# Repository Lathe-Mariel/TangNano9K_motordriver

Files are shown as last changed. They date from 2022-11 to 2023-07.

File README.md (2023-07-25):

# TangNano9K_Motordriver Board
  
Tang Nano 9K(Sipeed)用のマザーボード（拡張ボード）です．  
This is mother board for Tang Nano 9K(Sipeed).  

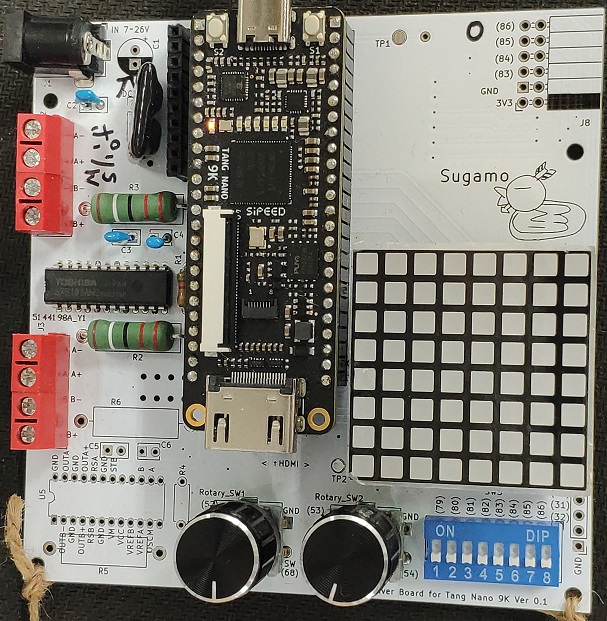
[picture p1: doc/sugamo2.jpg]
MotorDriver board for TangNano 9K
  
  
オープンソースの回路CADである，KiCAD のプロジェクトになっています．  
These files were made by KiCAD.
  
/doc ドキュメント用の素材  
/output　KiCADで出力したガーバーデータ  
/output/tangnano9k_motordriver-v3.zip　　PCBメーカにアップロードするファイル  
/sampleProject　この基板向けの数種類のサンプルプロジェクト  

## 機能 Functions
次の機能を実装できます．
- ステッピングモータドライバ x2ch <TB67S101ANG(TOSHIBA)>
- ロータリエンコーダ x2
- 8x8 マトリクスLED <OSL641501-BRA(Optsupply)>
- 7セグメントLED
- DIP Switch(8ch)

You can install these functions with this board.
- Stepper motor driver x2ch
- Rotary encoder x2
- 8x8 Matrix LED
- 7segment LED
- DIP Switch(8ch)

## 電源 Power supply
ボード上にDC-DCコンバータBP5293-50(ROHM)を実装できます．  
DC-DCコンバータには7～26Vを入力し，出力される5VをTang Nano 9Kへ供給できます．  
DC-DC converter can be installed on the board.  
  
基板上のDCジャックへ入力された電圧は，上記DC-DCコンバータとモータ・ドライバICのモータ電源（VM）へ入力されます．  
 
## FPGA側のピンを共用する機能 Multi purpose pins for board functions
　FPGAのピン数が限られているので，拡張ボードの持つ機能のうち，一部の機能は同時利用はできません．  
   
### HDMIコネクタとマトリクスLED＆ロータリ・エンコーダ×2
　DVI信号を出力する場合， `HDMI_CK_N(68)` ， `HDMI_CK_P(69)` ， `HDMI_D0` ～ `HDMI_D2` など8本の信号を使います．これらは，ロータリ・エンコーダ2ch目およびマトリクスLEDの信号と競合します．従ってDVI出力する場合は，ロータリ・エンコーダの2ch目とマトリクスLEDが使えません．  
  ボードにマトリクスLEDを実装するときは，必要に応じて脱着できるようにピンソケット経由にするのがお勧めです． 

### HDMIコネクタとマトリクスLED
　一部の信号を共有しています．HDMIコネクタから信号を出す場合はマトリクスLEDを取り付けない方がよいでしょう．  
 マトリクスLEDを実装するときは，ピンソケットを介して取り付けるのがお勧めです．そうすれば，マトリクスLEDを必要に応じて脱着できます．  
  
### 排他利用する機能の選択 Selection of exclusive functions
　モータドライバの励磁モード選択は `INA1` ， `INA2` ， `INB1` ， `INB2` 端子で行います．  
　2CH目（基板下側）のモータドライバは，ソルダジャンパ `JP1～JP4` をショートすると， `INA1～INB2` の全てがVCCに接続され，励磁モードが2相励磁に固定されます（この場合， `JP5～JP8` はオープンのままにする）．   
 　2ch目のモータドライバで1-2相励磁やW1-2相励磁を行いたい場合，ソルダジャンパ `JP5～JP8` をショートさせます．すると `INA1～INB2` がFPGAに接続されるので，FPGAからHi/Lowを制御できます．  
  　ちなみに1ch目のモータドライバについては，このようなソルダジャンパはありません． `INA1～INB2` は全てFPGAに直結されているので，どの様な励磁モードを使う場合でも，FPGAから制御する必要があります．  
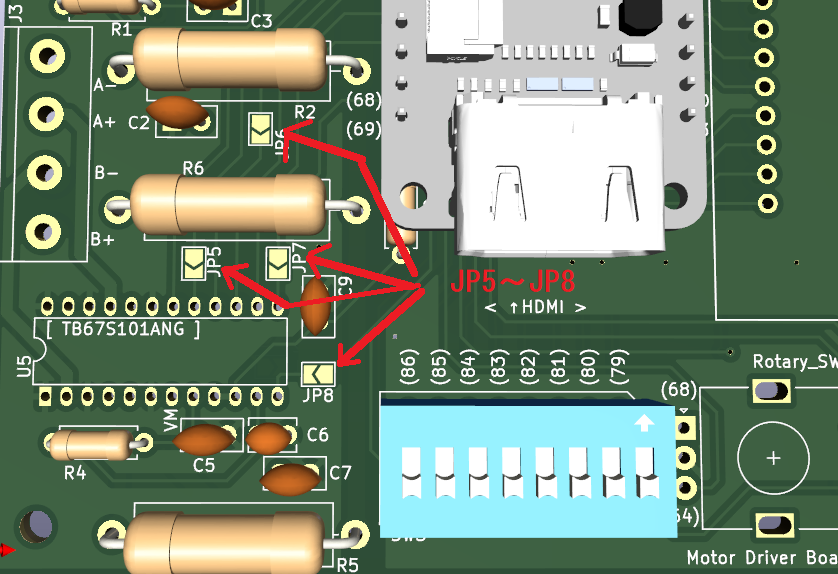
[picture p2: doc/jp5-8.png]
ソルダジャンパで選択する
  
  FPGA側では，これらの端子をロータリエンコーダの2ch目と共有しています．  
  従って，モータドライバの2ch目の1-2相励磁選択と，ロータリエンコーダの2ch目は排他利用となります．  
#### 設定例
　①例えば，モータドライバを1chしか使わない場合は， `JP1～JP8` のソルダジャンパをオープンのまま使用します（7セグLEDを使うなら `JP9` のみショートする）．  
 　②例えば，モータドライバの2ch目を1-2相励磁（あるいはW1-2相励磁）で使いたい場合は， `JP5～JP8` のソルダジャンパをショートします（ `INA1～INB2` がFPGAと直結される）．  
  この場合7セグLEDとロータリエンコーダの2ch目は使用できません（実装もしない方がよいでしょう）．  

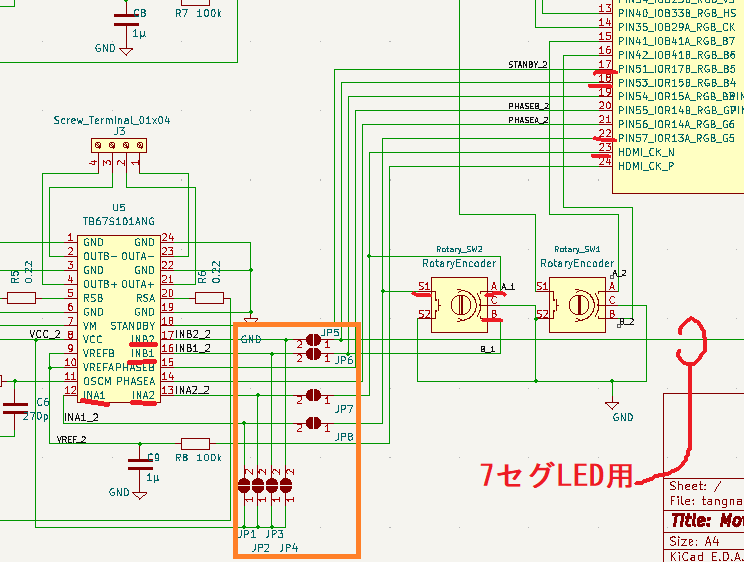
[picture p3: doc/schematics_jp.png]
JP1～JP4またはJP5～JP8のどちらかのセットをショートさせる

- JP1 ～ JP4　　ショートさせるとINA1～INB2をTB67S101ANGのVCCピンと接続
- JP5 ～ JP8　　ショートさせるとFPGAとINA1～INB2を接続
- JP9　　JP5の線を7セグLEDのコモンに接続
- JP10 ～ JP17　　マトリクスLEDに（アノード側）電流制限抵抗を付けない場合は，これらのソルダージャンパをショートさせてください  

## マトリクスLED MatrixLED
　~増幅回路も電流制限抵抗も入れていません．~  
　~ワイルドだろぅ？~  
  電流制限抵抗を入れない場合は，ソルダージャンパ `JP10` ～ `JP17` をジャンパします．
　必要であれば，FPGA側のロジックで絞ってください．  
　特に絞らずに使っていますが，LEDもFPGAも壊れないようです．  
  
  電流制限抵抗を入れる場合は，ソルダージャンパ `JP10` ～ `JP17` はオープンなまま抵抗器を実装します．  
トランジスタなどのパターンは基板にありません．電流を増幅せずに，真面目に計算して電流制限抵抗を入れると，LEDがかなり暗くなるようです．  

### マトリクスLED取り付け向き
  LED_direction

## 部品
　思いつく限り列挙．抜けがあるかもしれない．  
 ロータリエンコーダのみ，押しスイッチ付きのものが秋月さんに見当たらなかったので，リストに入っていません．  
 基板の4角には穴が開いています．足としてM3程度のボルト・ナットを用意するとよいでしょう．M3だときついのですが，ねじ込めば入ります．  
 （モータドライブ回路用の部品は1ch分の数量を掲載している）
　ちなみに，秋月さんの店頭に出ていない部品もあります（モータドライバなどは，裏オプションなので，お店の人に言うと裏から出してくれます）．
   
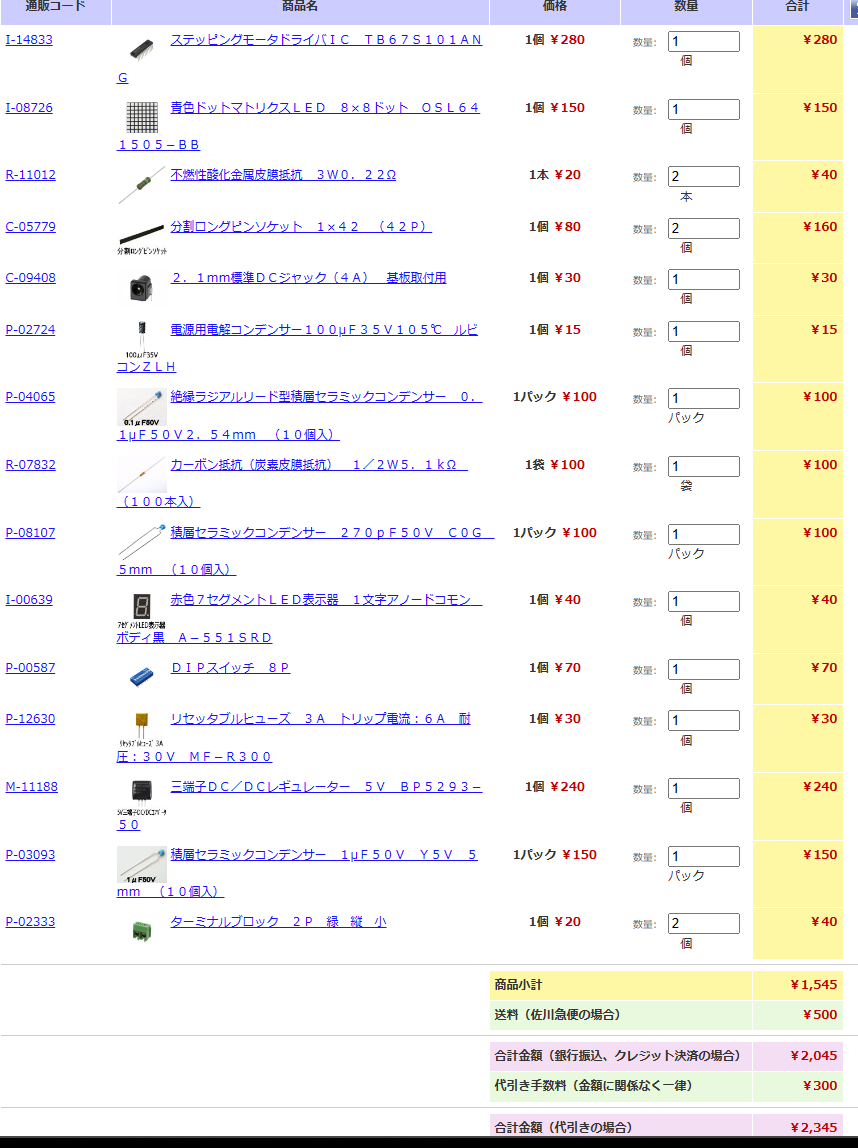
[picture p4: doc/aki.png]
参考部品リスト
 
 
## 機能の補足 Additional for Functions
### モータドライバTB67S101ANG（TOSHIBA）
　このICへ電流制御用のレファレンス電圧を供給する必要があります．Pinは `VREFA` 及び `VREFB` です．このボードでは `VREFA` と `VREFB` は直結されています．これらとFPGAの `27` （モータドライバch1）が接続されています．FPGAからパルスのデューティで所望の電圧を送って下さい．電圧の平滑化のために，RCフィルタのパターンが実装されています．R7とC8（モータドライバch1）に適当な値のものを実装してください．  
 （RCは，1μFと100kオーム．duty3/8くらいから試してください）  

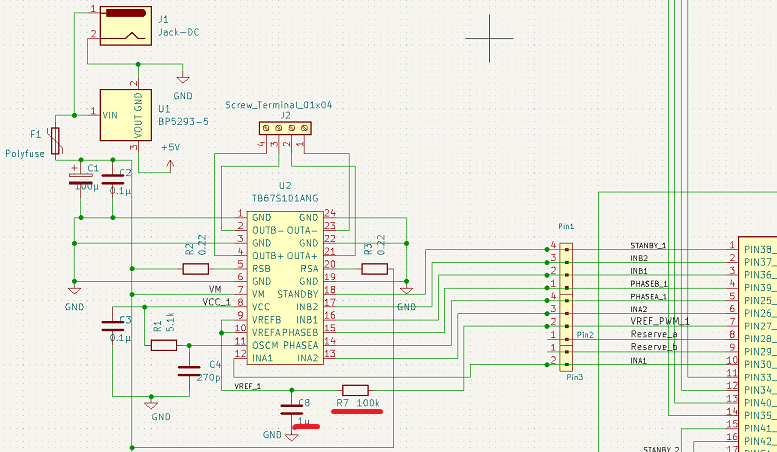
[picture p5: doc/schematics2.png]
モータドライバのレファレンス電圧供給経路にあるRCフィルタ
   

## サンプルプログラム
   
### PolyphonyMatrix_Clock
`/sampleProject`にマトリクスLEDを使った時計のプロジェクトが入っています．  
このプロジェクトはPythonベースの高位合成ツールPolyphonyを利用しています．  
　Gowin EDAのプロジェクトになっているので，そのままGowin EDAで読み込めます．impl/pnr/にビットストリームファイルもあるので，合成しなくてもすぐにFlash Programmerで書き込めます．  
 Verilogファイル `LEDMatrixAB_m.v` は，Polyphonyで `LEDMatrix.py` をコンパイルして生成したものです．
 
### MotorDriver
 モータドライバ IC TB67S101ANG(TOSHIBA) を使ってステッピングモータの2相励磁，1－2相励磁，W1-2相励磁ができます． 
 このサンプルプログラムでは，DVI出力もしています．ピンが競合するのでマトリクスLEDは取り外してください．  
#### DVI出力
　DVI出力については，Interface誌2022年12月号　別冊付録Gowin　の応用編第3章の記事で紹介されたデザインをパクり，一部を改変しています（SPDXライセンス）．  

### Parallel
　回路を複数のモジュールに分けて並列に実行させるサンプルです．3つのLEDを3つの回路で点滅させています．  
  
 （1）TB67S101ANGデータシート  
 https://toshiba.semicon-storage.com/jp/semiconductor/product/motor-driver-ics/stepping-motor-driver-ics/detail.TB67S101ANG.html

# Schematics
https://kicanvas.org/?github=https%3A%2F%2Fgithub.com%2FLathe-Mariel%2FTangNano9K_motordriver%2Ftree%2Fmain

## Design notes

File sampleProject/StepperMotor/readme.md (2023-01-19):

  
## 励磁モードは3つ用意してある There're 3types of excitation mode
|File|content|
|---|---|
src/Motor_12.sv | 1－2相励磁　駆動モジュール  
src/Motor_w12.sv | W1－2相励磁　駆動モジュール  
src/Motor_2.sv | 2相励磁　駆動モジュール  
src/top_w12.sv | トップモジュール  
src/top.cst | MotorDriver Board for TangNano9K用物理制約ファイル  
src/StepperMotor.rao | 
impl/pnr/a0_0.fs | GAO用ビットストリーム
impl/pnr/StepperMotor.fs | ビットストリーム
  
3つある駆動モジュールのインターフェースは全て同じなので容易に入れ替えできます．  
Because of same interface, You can easily swap motor driver module.  
  
### 駆動モジュールのインターフェース

  input  wire       clk,　　システムクロック（←トップモジュール）  
  output logic      phase_a,　　A相コイル（→ドライバIC）  
  output logic      phase_b,　　B相コイル（→ドライバIC）  
  output logic      INB1,　　INB1信号（→ドライバIC）  
  output logic      INB2,　　INB2信号（→ドライバIC）  
  output logic      INA1,　　INA1信号（→ドライバIC）  
  output logic      INA2,　　INA2信号（→ドライバIC）  
  output logic      STANBY,　　スタンバイ（→ドライバIC）　ONでドライバICがレディ（レディ状態で，回転指令がないの場合はロータ位置を保持）  
  output logic      VREF_PWM,　　電流設定用の電圧をdutyで出力（→ドライバIC）　ボード上にRCフィルタ有り  
  input  wire       rotate_pulse,　　回転速度指令（←トップモジュール）  
  input  wire       direction,　　回転方向指令  （←トップモジュール）  
  input  wire       module_enable,　　モジュール・イネーブル指令（←トップモジュール）  
  input  wire[3:0]       vref_level　　駆動電流値指令　｛0～15の16段階｝  （←トップモジュール）  
    
  モジュールへの指令は下段の4つの信号で行います．  
  top.svモジュールからこの4つの信号を使って指令すれば，このモジュール内でモータドライバICへ送る信号が生成されます．  

ステッピングモータの回転　1ステップを `rotate_pulse` で指令します．  
3つある駆動モジュールそれぞれの1ステップに対する機械角は1：2：4（2相/1-2相/W1-2相）になります．  
これらを統一するため， `Motor_2.sv` モジュール内では， `rotate_pulse` を4分周しています．  
同様に， `Motor_12.sv` モジュール内では2分周しています．  
これによって，どのモジュールであっても，同じ周波数のパルスを `rotate_pulse` に与えれば，モータは同じ機械角速度で回転します．

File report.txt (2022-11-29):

Info: Processing symbol 'C1:Capacitor_THT:CP_Radial_D5.0mm_P2.50mm'.
Info: Processing symbol 'C6:Capacitor_THT:C_Disc_D3.8mm_W2.6mm_P2.50mm'.
Info: Processing symbol 'SW3:Button_Switch_THT:SW_DIP_SPSTx08_Slide_9.78x22.5mm_W7.62mm_P2.54mm'.
Info: Processing symbol 'J6:Connector_PinHeader_2.54mm:PinHeader_1x02_P2.54mm_Vertical'.
Info: Processing symbol 'C4:Capacitor_THT:C_Disc_D3.8mm_W2.6mm_P2.50mm'.
Info: Processing symbol 'R2:Resistor_THT:R_Axial_DIN0516_L15.5mm_D5.0mm_P20.32mm_Horizontal'.
Info: Processing symbol 'R3:Resistor_THT:R_Axial_DIN0516_L15.5mm_D5.0mm_P20.32mm_Horizontal'.
Info: Processing symbol 'R1:Resistor_THT:R_Axial_DIN0207_L6.3mm_D2.5mm_P7.62mm_Horizontal'.
Info: Processing symbol 'R6:Resistor_THT:R_Axial_DIN0516_L15.5mm_D5.0mm_P20.32mm_Horizontal'.
Info: Processing symbol 'R4:Resistor_THT:R_Axial_DIN0207_L6.3mm_D2.5mm_P7.62mm_Horizontal'.
Info: Processing symbol 'C2:Capacitor_THT:C_Disc_D5.0mm_W2.5mm_P2.50mm'.
Info: Processing symbol 'SW1:Rotary_Encoder:RotaryEncoder_Alps_EC11E-Switch_Vertical_H20mm'.
Info: Processing symbol 'J1:Connector_BarrelJack:BarrelJack_Horizontal'.
Info: Processing symbol 'R5:Resistor_THT:R_Axial_DIN0516_L15.5mm_D5.0mm_P20.32mm_Horizontal'.
Info: Processing symbol 'C5:Capacitor_THT:C_Disc_D5.0mm_W2.5mm_P2.50mm'.
Info: Processing symbol 'SW2:Rotary_Encoder:RotaryEncoder_Alps_EC11E-Switch_Vertical_H20mm'.
Info: Processing symbol 'TP1:TestPoint:TestPoint_Pad_D2.0mm'.
Info: Processing symbol 'J7:Connector_PinHeader_2.54mm:PinHeader_1x04_P2.54mm_Vertical'.
Info: Processing symbol 'C3:Capacitor_THT:C_Disc_D5.0mm_W2.5mm_P2.50mm'.
Info: Processing symbol 'J4:Connector_PinHeader_2.54mm:PinHeader_1x04_P2.54mm_Vertical'.
Info: Processing symbol 'J3:TerminalBlock:TerminalBlock_bornier-4_P5.08mm'.
Info: Processing symbol 'J5:Connector_PinHeader_2.54mm:PinHeader_1x04_P2.54mm_Vertical'.
Info: Processing symbol 'TP2:TestPoint:TestPoint_Pad_D2.0mm'.
Info: Processing symbol 'J2:TerminalBlock:TerminalBlock_bornier-4_P5.08mm'.
Info: Processing symbol 'U1:Connector_PinHeader_2.54mm:PinHeader_1x04_P2.54mm_Vertical'.
Info: Processing symbol 'U2:Motors:TB67S101ANG'.
Info: Processing symbol 'U3:Package_DIP:Tang_Nano_9K'.
Info: Processing symbol 'U4:LED_THT:OSL641501-ARA'.
Info: Processing symbol 'U5:Motors:TB67S101ANG'.
Add net Net-(C1-Pad1).
Connected C1 pin 1 to Net-(C1-Pad1).
Add net GND.
Connected C1 pin 2 to GND.
Added C2 (footprint 'Capacitor_THT:C_Disc_D5.0mm_W2.5mm_P2.50mm').
Changed REF** reference designator to C2.
Changed C2 value from C_Disc_D5.0mm_W2.5mm_P2.50mm to 0.1μ.
Updated C2 symbol association from  to /f88607f0-b8ca-451c-9113-0f5bf3405953.
Updated C2 properties.
Connected C2 pin 1 to Net-(C1-Pad1).
Connected C2 pin 2 to GND.
Added C3 (footprint 'Capacitor_THT:C_Disc_D5.0mm_W2.5mm_P2.50mm').
Changed REF** reference designator to C3.
Changed C3 value from C_Disc_D5.0mm_W2.5mm_P2.50mm to 0.1μ.
Updated C3 symbol association from  to /03905288-6954-4141-9c45-1c11764a1ca3.
Updated C3 properties.
Add net Net-(C3-Pad1).
Connected C3 pin 1 to Net-(C3-Pad1).
Connected C3 pin 2 to GND.
Added C4 (footprint 'Capacitor_THT:C_Disc_D3.8mm_W2.6mm_P2.50mm').
Changed REF** reference designator to C4.
Changed C4 value from C_Disc_D3.8mm_W2.6mm_P2.50mm to 270p.
Updated C4 symbol association from  to /3f9d012d-84b1-4698-b5f7-e431ed62cc93.
Updated C4 properties.
Add net Net-(C4-Pad1).
Connected C4 pin 1 to Net-(C4-Pad1).
Connected C4 pin 2 to GND.
Added C5 (footprint 'Capacitor_THT:C_Disc_D5.0mm_W2.5mm_P2.50mm').
Changed REF** reference designator to C5.
Changed C5 value from C_Disc_D5.0mm_W2.5mm_P2.50mm to 0.1μ.
Updated C5 symbol association from  to /71d9e1f5-0827-4510-b811-be115d614ba5.
Updated C5 properties.
Add net Net-(C5-Pad1).
Connected C5 pin 1 to Net-(C5-Pad1).
Connected C5 pin 2 to GND.
Added C6 (footprint 'Capacitor_THT:C_Disc_D3.8mm_W2.6mm_P2.50mm').
Changed REF** reference designator to C6.
Changed C6 value from C_Disc_D3.8mm_W2.6mm_P2.50mm to 270p.
Updated C6 symbol association from  to /ed01aafb-4cf2-4f1f-b1c7-63d4035ca6df.
Updated C6 properties.
Add net Net-(C6-Pad1).
Connected C6 pin 1 to Net-(C6-Pad1).
Connected C6 pin 2 to GND.
Added J1 (footprint 'Connector_BarrelJack:BarrelJack_Horizontal').
Changed REF** reference designator to J1.
Changed J1 value from BarrelJack_Horizontal to Jack-DC.
Updated J1 symbol association from  to /c4ef8bf0-b9fa-40d3-ad8d-56b46e78b9a1.
Updated J1 properties.
Connected J1 pin 1 to Net-(C1-Pad1).
Connected J1 pin 2 to GND.
Added J2 (footprint 'TerminalBlock:TerminalBlock_bornier-4_P5.08mm').
Changed REF** reference designator to J2.
Changed J2 value from TerminalBlock_bornier-4_P5.08mm to Screw_Terminal_01x04.
Updated J2 symbol association from  to /6e56f2a7-8754-4162-80c8-542615da19fa.
Updated J2 properties.
Add net Net-(J2-Pad1).
Connected J2 pin 1 to Net-(J2-Pad1).
Add net Net-(J2-Pad2).
Connected J2 pin 2 to Net-(J2-Pad2).
Add net Net-(J2-Pad3).
Connected J2 pin 3 to Net-(J2-Pad3).
Add net Net-(J2-Pad4).
Connected J2 pin 4 to Net-(J2-Pad4).
Added J3 (footprint 'TerminalBlock:TerminalBlock_bornier-4_P5.08mm').
Changed REF** reference designator to J3.
Changed J3 value from TerminalBlock_bornier-4_P5.08mm to Screw_Terminal_01x04.
Updated J3 symbol association from  to /cfdb3be4-9e51-4291-aaa9-423f861aa8fe.
Updated J3 properties.
Add net Net-(J3-Pad1).
Connected J3 pin 1 to Net-(J3-Pad1).
Add net Net-(J3-Pad2).
Connected J3 pin 2 to Net-(J3-Pad2).
Add net Net-(J3-Pad3).
Connected J3 pin 3 to Net-(J3-Pad3).
Add net Net-(J3-Pad4).
Connected J3 pin 4 to Net-(J3-Pad4).
Added J4 (footprint 'Connector_PinHeader_2.54mm:PinHeader_1x04_P2.54mm_Vertical').
Changed REF** reference designator to J4.
Changed J4 value from PinHeader_1x04_P2.54mm_Vertical to Reserve.
Updated J4 symbol association from  to /2bd52874-4404-4e06-8e0b-da7441e79232.
Updated J4 properties.
Add net /STANBY_1.
Connected J4 pin 1 to /STANBY_1.
Add net /VREF_1.
Connected J4 pin 2 to /VREF_1.
Add net /PHASEB_1.
Connected J4 pin 3 to /PHASEB_1.
Add net /PHASEA_1.
Connected J4 pin 4 to /PHASEA_1.
Added J5 (footprint 'Connector_PinHeader_2.54mm:PinHeader_1x04_P2.54mm_Vertical').
Changed REF** reference designator to J5.
Changed J5 value from PinHeader_1x04_P2.54mm_Vertical to Reserve.
Updated J5 symbol association from  to /15a4aca8-8327-4160-a767-e7952a84c3b4.
Updated J5 properties.
Add net /STANBY_2.
Connected J5 pin 1 to /STANBY_2.
Add net /VREF_2.
Connected J5 pin 2 to /VREF_2.
Add net /PHASEB_2.
Connected J5 pin 3 to /PHASEB_2.
Add net /PHASEA_2.
Connected J5 pin 4 to /PHASEA_2.
Added J6 (footprint 'Connector_PinHeader_2.54mm:PinHeader_1x02_P2.54mm_Vertical').
Changed REF** reference designator to J6.
Changed J6 value from PinHeader_1x02_P2.54mm_Vertical to Reserve.
Updated J6 symbol association from  to /245cba81-c999-4f09-adfa-29dd70da9f7e.
Updated J6 properties.
Add net Net-(J6-Pad1).
Connected J6 pin 1 to Net-(J6-Pad1).
Add net Net-(J6-Pad2).
Connected J6 pin 2 to Net-(J6-Pad2).
Added J7 (footprint 'Connector_PinHeader_2.54mm:PinHeader_1x04_P2.54mm_Vertical').
Changed REF** reference designator to J7.
Changed J7 value from PinHeader_1x04_P2.54mm_Vertical to Reserve_PinHeader.
Updated J7 symbol association from  to /d103ad51-1bb4-491e-8354-64c6e089e9f1.
Updated J7 properties.
Add net Net-(J7-Pad1).
Connected J7 pin 1 to Net-(J7-Pad1).
Add net Net-(J7-Pad2).
Connected J7 pin 2 to Net-(J7-Pad2).
Add net Net-(J7-Pad3).
Connected J7 pin 3 to Net-(J7-Pad3).
Add net Net-(J7-Pad4).
Connected J7 pin 4 to Net-(J7-Pad4).
Added R1 (footprint 'Resistor_THT:R_Axial_DIN0207_L6.3mm_D2.5mm_P7.62mm_Horizontal').
Changed REF** reference designator to R1.
Changed R1 value from R_Axial_DIN0207_L6.3mm_D2.5mm_P7.62mm_Horizontal to 5.1k.
Updated R1 symbol association from  to /02021ba7-4d1a-4846-a4b4-00321b415f7f.
Updated R1 properties.
Connected R1 pin 1 to Net-(C3-Pad1).
Connected R1 pin 2 to Net-(C4-Pad1).
Added R2 (footprint 'Resistor_THT:R_Axial_DIN0516_L15.5mm_D5.0mm_P20.32mm_Horizontal').
Changed REF** reference designator to R2.
Changed R2 value from R_Axial_DIN0516_L15.5mm_D5.0mm_P20.32mm_Horizontal to 0.22.
Updated R2 symbol association from  to /e506dbf7-f368-4b31-b332-791a536c5ddc.
Updated R2 properties.
Connected R2 pin 1 to Net-(C1-Pad1).
Add net Net-(R2-Pad2).
Connected R2 pin 2 to Net-(R2-Pad2).
Added R3 (footprint 'Resistor_THT:R_Axial_DIN0516_L15.5mm_D5.0mm_P20.32mm_Horizontal').
Changed REF** reference designator to R3.
Changed R3 value from R_Axial_DIN0516_L15.5mm_D5.0mm_P20.32mm_Horizontal to 0.22.
Updated R3 symbol association from  to /fe3d4578-0dfd-4336-86c5-0e51ed900e50.
Updated R3 properties.
Add net Net-(R3-Pad1).
Connected R3 pin 1 to Net-(R3-Pad1).
Connected R3 pin 2 to Net-(C1-Pad1).
Added R4 (footprint 'Resistor_THT:R_Axial_DIN0207_L6.3mm_D2.5mm_P7.62mm_Horizontal').
Changed REF** reference designator to R4.
Changed R4 value from R_Axial_DIN0207_L6.3mm_D2.5mm_P7.62mm_Horizontal to 5.1k.
Updated R4 symbol association from  to /ace3803d-3737-46c9-af27-dd8dd29ce29b.
Updated R4 properties.
Connected R4 pin 1 to Net-(C5-Pad1).
Connected R4 pin 2 to Net-(C6-Pad1).
Added R5 (footprint 'Resistor_THT:R_Axial_DIN0516_L15.5mm_D5.0mm_P20.32mm_Horizontal').
Changed REF** reference designator to R5.
Changed R5 value from R_Axial_DIN0516_L15.5mm_D5.0mm_P20.32mm_Horizontal to 0.22.
Updated R5 symbol association from  to /1021c236-df86-4235-8f73-6637bea80569.
Updated R5 properties.
Connected R5 pin 1 to Net-(C1-Pad1).
Add net Net-(R5-Pad2).
Connected R5 pin 2 to Net-(R5-Pad2).
Added R6 (footprint 'Resistor_THT:R_Axial_DIN0516_L15.5mm_D5.0mm_P20.32mm_Horizontal').
Changed REF** reference designator to R6.
Changed R6 value from R_Axial_DIN0516_L15.5mm_D5.0mm_P20.32mm_Horizontal to 0.22.
Updated R6 symbol association from  to /4b91168f-7f0e-4cc2-9d41-9a841282bb5c.
Updated R6 properties.
Add net Net-(R6-Pad1).
Connected R6 pin 1 to Net-(R6-Pad1).
Connected R6 pin 2 to Net-(C1-Pad1).
Added SW1 (footprint 'Rotary_Encoder:RotaryEncoder_Alps_EC11E-Switch_Vertical_H20mm').
Changed REF** reference designator to SW1.
Changed SW1 value from RotaryEncoder_Alps_EC11E-Switch_Vertical_H20mm to RotaryEncoder.
Updated SW1 symbol association from  to /de986ad9-2077-4374-9035-245917b4b7a6.
Updated SW1 properties.
Add net /A_1.
Connected SW1 pin A to /A_1.
Add net /B_1.
Connected SW1 pin B to /B_1.
Connected SW1 pin C to GND.
Add net Net-(SW1-PadS1).
Connected SW1 pin S1 to Net-(SW1-PadS1).
Connected SW1 pin S2 to GND.
Added SW2 (footprint 'Rotary_Encoder:RotaryEncoder_Alps_EC11E-Switch_Vertical_H20mm').
Changed REF** reference designator to SW2.
Changed SW2 value from RotaryEncoder_Alps_EC11E-Switch_Vertical_H20mm to RotaryEncoder.
Updated SW2 symbol association from  to /266f7da2-d095-4158-b55b-54efc0936b08.
Updated SW2 properties.
Add net /A_2.
Connected SW2 pin A to /A_2.
Add net /B_2.
Connected SW2 pin B to /B_2.
Connected SW2 pin C to GND.
Add net Net-(SW2-PadS1).
Connected SW2 pin S1 to Net-(SW2-PadS1).
Connected SW2 pin S2 to GND.
Added SW3 (footprint 'Button_Switch_THT:SW_DIP_SPSTx08_Slide_9.78x22.5mm_W7.62mm_P2.54mm').
Changed REF** reference designator to SW3.
Changed SW3 value from SW_DIP_SPSTx08_Slide_9.78x22.5mm_W7.62mm_P2.54mm to SW_DIP_x08.
Updated SW3 symbol association from  to /0aaa49ea-91cb-46ee-9047-c501634b853b.
Updated SW3 properties.
Add net Net-(SW3-Pad1).
Connected SW3 pin 1 to Net-(SW3-Pad1).
Add net Net-(SW3-Pad2).
Connected SW3 pin 2 to Net-(SW3-Pad2).
Add net Net-(SW3-Pad3).
Connected SW3 pin 3 to Net-(SW3-Pad3).
Add net Net-(SW3-Pad4).
Connected SW3 pin 4 to Net-(SW3-Pad4).
Add net Net-(SW3-Pad5).
Connected SW3 pin 5 to Net-(SW3-Pad5).
Add net Net-(SW3-Pad6).
Connected SW3 pin 6 to Net-(SW3-Pad6).
Add net Net-(SW3-Pad7).
Connected SW3 pin 7 to Net-(SW3-Pad7).
Add net Net-(SW3-Pad8).
Connected SW3 pin 8 to Net-(SW3-Pad8).
Connected SW3 pin 9 to GND.
Connected SW3 pin 10 to GND.
Connected SW3 pin 11 to GND.
Connected SW3 pin 12 to GND.
Connected SW3 pin 13 to GND.
Connected SW3 pin 14 to GND.
Connected SW3 pin 15 to GND.
Connected SW3 pin 16 to GND.
Added TP1 (footprint 'TestPoint:TestPoint_Pad_D2.0mm').
Changed REF** reference designator to TP1.
Changed TP1 value from TestPoint_Pad_D2.0mm to TestPoint.
Updated TP1 symbol association from  to /b4b6c71b-c8e5-4172-96e6-29540545f271.
Updated TP1 properties.
Removed TP1 'exclude from BOM' fabrication attribute.
Add net Net-(TP1-Pad1).
Connected TP1 pin 1 to Net-(TP1-Pad1).
Added TP2 (footprint 'TestPoint:TestPoint_Pad_D2.0mm').
Changed REF** reference designator to TP2.
Changed TP2 value from TestPoint_Pad_D2.0mm to TestPoint.
Updated TP2 symbol association from  to /246ca8c3-d91c-4b19-a6a8-48a0cdc00a94.
Updated TP2 properties.
Removed TP2 'exclude from BOM' fabrication attribute.
Add net Net-(TP2-Pad1).
Connected TP2 pin 1 to Net-(TP2-Pad1).
Added C1 (footprint 'Capacitor_THT:CP_Radial_D5.0mm_P2.50mm').
Added U1 (footprint 'Connector_PinHeader_2.54mm:PinHeader_1x04_P2.54mm_Vertical').
Changed REF** reference designator to U1.
Changed U1 value from PinHeader_1x04_P2.54mm_Vertical to BP5293-5.
Updated U1 symbol association from  to /0555d286-6d86-4552-94e8-d32676b671db.
Updated U1 properties.
Connected U1 pin 1 to Net-(C1-Pad1).
Connected U1 pin 2 to GND.
Add net +5V.
Connected U1 pin 3 to +5V.
Changed REF** reference designator to C1.
Added U2 (footprint 'Motors:TB67S101ANG').
Changed REF** reference designator to U2.
Updated U2 symbol association from  to /3b4c24e8-0a83-40bc-8bf5-8923992c8f7f.
Updated U2 properties.
Connected U2 pin 1 to GND.
Connected U2 pin 2 to Net-(J2-Pad3).
Connected U2 pin 3 to GND.
Connected U2 pin 4 to Net-(J2-Pad4).
Connected U2 pin 5 to Net-(R2-Pad2).
Connected U2 pin 6 to GND.
Connected U2 pin 7 to Net-(C1-Pad1).
Connected U2 pin 8 to Net-(C3-Pad1).
Connected U2 pin 9 to /VREF_1.
Connected U2 pin 10 to /VREF_1.
Connected U2 pin 11 to Net-(C4-Pad1).
Connected U2 pin 12 to Net-(C3-Pad1).
Connected U2 pin 13 to Net-(C3-Pad1).
Connected U2 pin 14 to /PHASEA_1.
Connected U2 pin 15 to /PHASEB_1.
Connected U2 pin 16 to Net-(C3-Pad1).
Connected U2 pin 17 to Net-(C3-Pad1).
Connected U2 pin 18 to /STANBY_1.
Connected U2 pin 19 to GND.
Connected U2 pin 20 to Net-(R3-Pad1).
Connected U2 pin 21 to Net-(J2-Pad2).
Connected U2 pin 22 to GND.
Connected U2 pin 23 to Net-(J2-Pad1).
Connected U2 pin 24 to GND.
Changed C1 value from CP_Radial_D5.0mm_P2.50mm to 100μ.
Added U3 (footprint 'Package_DIP:Tang_Nano_9K').
Changed REF** reference designator to U3.
Changed U3 value from Tang Nano 9K to TangNano9K.
Updated U3 symbol association from  to /b07c7a86-f5e1-435b-90e8-dd8e473e3c0e.
Updated U3 properties.
Connected U3 pin 1 to /PHASEA_1.
Connected U3 pin 2 to /PHASEB_1.
Connected U3 pin 3 to /VREF_1.
Connected U3 pin 4 to /STANBY_1.
Connected U3 pin 5 to /PHASEA_2.
Connected U3 pin 6 to /PHASEB_2.
Connected U3 pin 7 to /VREF_2.
Connected U3 pin 8 to /STANBY_2.
Connected U3 pin 9 to Net-(J6-Pad2).
Add net Net-(U3-Pad10).
Connected U3 pin 10 to Net-(U3-Pad10).
Add net Net-(U3-Pad11).
Connected U3 pin 11 to Net-(U3-Pad11).
Add net Net-(U3-Pad12).
Connected U3 pin 12 to Net-(U3-Pad12).
Add net Net-(U3-Pad13).
Connected U3 pin 13 to Net-(U3-Pad13).
Add net Net-(U3-Pad14).
Connected U3 pin 14 to Net-(U3-Pad14).
Add net Net-(U3-Pad15).
Connected U3 pin 15 to Net-(U3-Pad15).
Add net Net-(U3-Pad16).
Connected U3 pin 16 to Net-(U3-Pad16).
Add net Net-(U3-Pad17).
Connected U3 pin 17 to Net-(U3-Pad17).
Connected U3 pin 18 to /A_2.
Connected U3 pin 19 to Net-(SW2-PadS1).
Connected U3 pin 20 to /B_2.
Connected U3 pin 21 to Net-(J6-Pad1).
Connected U3 pin 22 to /A_1.
Connected U3 pin 23 to Net-(SW1-PadS1).
Connected U3 pin 24 to /B_1.
Connected U3 pin 25 to Net-(TP2-Pad1).
Connected U3 pin 26 to GND.
Connected U3 pin 27 to Net-(J7-Pad1).
Connected U3 pin 28 to Net-(J7-Pad2).
Connected U3 pin 29 to Net-(J7-Pad3).
Connected U3 pin 30 to Net-(J7-Pad4).
Connected U3 pin 31 to +5V.
Add net Net-(U3-Pad32).
Connected U3 pin 32 to Net-(U3-Pad32).
Add net Net-(U3-Pad33).
Connected U3 pin 33 to Net-(U3-Pad33).
Add net Net-(U3-Pad34).
Connected U3 pin 34 to Net-(U3-Pad34).
Add net Net-(U3-Pad35).
Connected U3 pin 35 to Net-(U3-Pad35).
Add net Net-(U3-Pad36).
Connected U3 pin 36 to Net-(U3-Pad36).
Add net Net-(U3-Pad37).
Connected U3 pin 37 to Net-(U3-Pad37).
Add net Net-(U3-Pad38).
Connected U3 pin 38 to Net-(U3-Pad38).
Add net Net-(U3-Pad39).
Connected U3 pin 39 to Net-(U3-Pad39).
Connected U3 pin 40 to Net-(SW3-Pad8).
Connected U3 pin 41 to Net-(SW3-Pad7).
Connected U3 pin 42 to Net-(SW3-Pad6).
Connected U3 pin 43 to Net-(SW3-Pad5).
Connected U3 pin 44 to Net-(SW3-Pad4).
Connected U3 pin 45 to Net-(SW3-Pad3).
Connected U3 pin 46 to Net-(SW3-Pad2).
Connected U3 pin 47 to Net-(SW3-Pad1).
Connected U3 pin 48 to Net-(TP1-Pad1).
Updated C1 symbol association from  to /1b203025-f9a0-4031-a2eb-97e7f134dcdb.
Added U4 (footprint 'LED_THT:OSL641501-ARA').
Changed REF** reference designator to U4.
Changed U4 value from OSL641501-ARA to OSL641505-BB.
Updated U4 symbol association from  to /467c1fba-20c5-4c47-a5bb-8b74d3cc9c21.
Updated U4 properties.
Connected U4 pin 1 to Net-(U3-Pad32).
Connected U4 pin 2 to Net-(U3-Pad33).
Connected U4 pin 3 to Net-(U3-Pad34).
Connected U4 pin 4 to Net-(U3-Pad35).
Connected U4 pin 5 to Net-(U3-Pad36).
Connected U4 pin 6 to Net-(U3-Pad37).
Connected U4 pin 7 to Net-(U3-Pad38).
Connected U4 pin 8 to Net-(U3-Pad39).
Connected U4 pin 9 to Net-(U3-Pad10).
Connected U4 pin 10 to Net-(U3-Pad11).
Connected U4 pin 11 to Net-(U3-Pad12).
Connected U4 pin 12 to Net-(U3-Pad13).
Connected U4 pin 13 to Net-(U3-Pad14).
Connected U4 pin 14 to Net-(U3-Pad15).
Connected U4 pin 15 to Net-(U3-Pad16).
Connected U4 pin 16 to Net-(U3-Pad17).
Updated C1 properties.
Added U5 (footprint 'Motors:TB67S101ANG').
Changed REF** reference designator to U5.
Updated U5 symbol association from  to /b5d87323-6270-4b62-ba18-02f5c393e6db.
Updated U5 properties.
Connected U5 pin 1 to GND.
Connected U5 pin 2 to Net-(J3-Pad3).
Connected U5 pin 3 to GND.
Connected U5 pin 4 to Net-(J3-Pad4).
Connected U5 pin 5 to Net-(R5-Pad2).
Connected U5 pin 6 to GND.
Connected U5 pin 7 to Net-(C1-Pad1).
Connected U5 pin 8 to Net-(C5-Pad1).
Connected U5 pin 9 to /VREF_2.
Connected U5 pin 10 to /VREF_2.
Connected U5 pin 11 to Net-(C6-Pad1).
Connected U5 pin 12 to Net-(C5-Pad1).
Connected U5 pin 13 to Net-(C5-Pad1).
Connected U5 pin 14 to /PHASEA_2.
Connected U5 pin 15 to /PHASEB_2.
Connected U5 pin 16 to Net-(C5-Pad1).
Connected U5 pin 17 to Net-(C5-Pad1).
Connected U5 pin 18 to /STANBY_2.
Connected U5 pin 19 to GND.
Connected U5 pin 20 to Net-(R6-Pad1).
Connected U5 pin 21 to Net-(J3-Pad2).
Connected U5 pin 22 to GND.
Connected U5 pin 23 to Net-(J3-Pad1).
Connected U5 pin 24 to GND.
Warning: No net found for symbol SW1 pin MP.
Warning: No net found for symbol J1 pin 3.
Warning: No net found for symbol SW1 pin MP.
Warning: No net found for symbol SW2 pin MP.
Warning: No net found for symbol SW2 pin MP.
Warning: No net found for symbol U1 pin 4.

Info: Total warnings: 0, errors: 0.

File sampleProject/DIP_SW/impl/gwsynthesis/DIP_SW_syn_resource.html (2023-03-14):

# Hierarchy Module Resource

MODULE NAME | REG NUMBER | ALU NUMBER | LUT NUMBER | DSP NUMBER | BSRAM NUMBER | SSRAM NUMBER
top (E:/git/TangNano9K_motordriver/sampleProject/DIP_SW/src/top.sv) | 9 | - | 16 | - | - | -
|--inst_1 (E:/git/TangNano9K_motordriver/sampleProject/DIP_SW/src/top.sv) | 25 | 23 | 9 | - | - | -

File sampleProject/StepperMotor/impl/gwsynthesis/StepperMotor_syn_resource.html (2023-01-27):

# Hierarchy Module Resource

MODULE NAME | REG NUMBER | ALU NUMBER | LUT NUMBER | DSP NUMBER | BSRAM NUMBER | SSRAM NUMBER
top_w12 (E:/git/TangNano9K_motordriver/sampleProject/StepperMotor/src/top_w12.sv) | 28 | - | 49 | - | - | -
|--inst_w12 (E:/git/TangNano9K_motordriver/sampleProject/StepperMotor/src/top_w12.sv) | 9 | 4 | 3 | - | - | -
|--inst_12 (E:/git/TangNano9K_motordriver/sampleProject/StepperMotor/src/top_w12.sv) | 4 | 4 | 4 | - | - | -
|--inst_2 (E:/git/TangNano9K_motordriver/sampleProject/StepperMotor/src/top_w12.sv) | 3 | 4 | 7 | - | - | -
|--timer_i (E:/git/TangNano9K_motordriver/sampleProject/StepperMotor/src/top_w12.sv) | 17 | 15 | 6 | - | - | -
|--reset_seq_ext (E:/git/TangNano9K_motordriver/sampleProject/StepperMotor/src/top_w12.sv) | 17 | - | - | - | - | -
|--rpll_dvi (E:/git/TangNano9K_motordriver/sampleProject/StepperMotor/src/top_w12.sv) | - | - | - | - | - | -
|--rpll_dvi_ser (E:/git/TangNano9K_motordriver/sampleProject/StepperMotor/src/top_w12.sv) | - | - | - | - | - | -
|--reset_seq_dvi (E:/git/TangNano9K_motordriver/sampleProject/StepperMotor/src/top_w12.sv) | 5 | - | - | - | - | -
|--tpg_inst (E:/git/TangNano9K_motordriver/sampleProject/StepperMotor/src/top_w12.sv) | 27 | 10 | 181 | - | - | -
|--dvi_out_inst (E:/git/TangNano9K_motordriver/sampleProject/StepperMotor/src/top_w12.sv) | 73 | 66 | 198 | - | - | -

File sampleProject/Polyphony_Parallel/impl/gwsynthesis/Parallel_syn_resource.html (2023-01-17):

# Hierarchy Module Resource

MODULE NAME | REG NUMBER | ALU NUMBER | LUT NUMBER | DSP NUMBER | BSRAM NUMBER | SSRAM NUMBER
top (E:/git/TangNano9K_motordriver/sampleProject/Polyphony_Parallel/src/top.sv) | 10 | 7 | 6 | - | - | -
|--inst (E:/git/TangNano9K_motordriver/sampleProject/Polyphony_Parallel/src/top.sv) | 142 | - | 282 | - | - | -
|--inst_1 (E:/git/TangNano9K_motordriver/sampleProject/Polyphony_Parallel/src/top.sv) | 25 | 23 | 9 | - | - | -

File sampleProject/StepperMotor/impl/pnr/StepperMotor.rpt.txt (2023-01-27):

//Copyright (C)2014-2022 Gowin Semiconductor Corporation.
//All rights reserved.

1. PnR Messages

  <Report Title>: PnR Report
  <Design File>: E:\git\TangNano9K_motordriver\sampleProject\StepperMotor\impl\gwsynthesis\StepperMotor.vg
  <Physical Constraints File>: E:\git\TangNano9K_motordriver\sampleProject\StepperMotor\src\top.cst
  <Timing Constraints File>: ---
  <PnR Version>: V1.9.8.09 Education
  <Part Number>: GW1NR-LV9QN88PC6/I5
  <Device>: GW1NR-9C
  <Created Time>:Thu Jan 26 13:42:43 2023

2. PnR Details

  Running placement:
    Placement Phase 0: CPU time = 0h 0m 0.173s, Elapsed time = 0h 0m 0.173s
    Placement Phase 1: CPU time = 0h 0m 0.007s, Elapsed time = 0h 0m 0.008s
    Placement Phase 2: CPU time = 0h 0m 0.043s, Elapsed time = 0h 0m 0.043s
    Placement Phase 3: CPU time = 0h 0m 2s, Elapsed time = 0h 0m 2s
    Total Placement: CPU time = 0h 0m 2s, Elapsed time = 0h 0m 2s
 Running routing:
    Routing Phase 0: CPU time = 0h 0m 0s, Elapsed time = 0h 0m 0s
    Routing Phase 1: CPU time = 0h 0m 0.12s, Elapsed time = 0h 0m 0.12s
    Routing Phase 2: CPU time = 0h 0m 0.359s, Elapsed time = 0h 0m 0.36s
    Total Routing: CPU time = 0h 0m 0.479s, Elapsed time = 0h 0m 0.48s
 Generate output files:
    CPU time = 0h 0m 0.77s, Elapsed time = 0h 0m 0.77s

 Total Time and Memory Usage: CPU time = 0h 0m 3s, Elapsed time = 0h 0m 3s, Peak memory usage = 192MB

3. Resource Usage Summary

  ----------------------------------------------------------
  Resources                   | Usage
  ----------------------------------------------------------
  Logic                       | 569/8640  6%
    --LUT,ALU,ROM16           | 569(443 LUT, 126 ALU, 0 ROM16)
    --SSRAM(RAM16)            | 0
  Register                    | 183/6693  2%
    --Logic Register as Latch | 0/6480  0%
    --Logic Register as FF    | 175/6480  2%
    --I/O Register as Latch   | 0/213  0%
    --I/O Register as FF      | 8/213  3%
  CLS                         | 337/4320  7%
  I/O Port                    | 25
  I/O Buf                     | 22
    --Input Buf               | 4
    --Output Buf              | 18
    --Inout Buf               | 0
  IOLOGIC                     | 8%
    --OSER10                  | 4
  BSRAM                       | 0%
  DSP                         | 0%
  PLL                         | 2/2  100%
  DCS                         | 0/8  0%
  DQCE                        | 0/24  0%
  OSC                         | 0/1  0%
  User Flash                  | 0/1  0%
  CLKDIV                      | 0/8  0%
  DLLDLY                      | 0/8  0%
  DHCEN                       | 0/8  0%
  DHCENC                      | 0/4  0%
  ==========================================================

4. I/O Bank Usage Summary

  -----------------------
  I/O Bank  | Usage       
  -----------------------
  bank 1   | 10/25(40%)  
  bank 2   | 12/23(52%)  
  bank 3   | 7/23(30%)   
  =======================

5. Global Clock Usage Summary

  -------------------------------
  Global Clock  | Usage       
  -------------------------------
  PRIMARY       | 3/8(37%)
  LW            | 1/8(12%)
  GCLK_PIN      | 2/4(50%)
  PLL           | 2/2(100%)
  CLKDIV        | 0/8(0%)
  DLLDLY        | 0/8(0%)
  ===============================

6. Global Clock Signals

  -------------------------------------------
  Signal         | Global Clock   | Location
  -------------------------------------------
  clk_d          | PRIMARY        |  TR BR BL
  motor_pulse_4  | PRIMARY        |  BL
  clock_dvi      | PRIMARY        |  TR TL BR BL
  reset_dvi      | LW             |  -
  clock_dvi_ser  | HCLK           | TOP[0]
  ===========================================

7. Pinout by Port Name

-----------------------------------------------------------------------------------------------------------------------------------------------------------------------------------------------------------------------
Port Name       | Diff Pair | Loc./Bank     | Constraint | Dir.  | Site     | IO Type    | Drive | Pull Mode | PCI Clamp | Hysteresis | Open Drain | Slew Rate | Vref       | Single Resistor | Diff Resistor | BankVccio 
-----------------------------------------------------------------------------------------------------------------------------------------------------------------------------------------------------------------------
clk             |           | 52/1          | Y          | in    | IOR17[A] | LVCMOS33   | NA    | UP        | ON        | NONE       | NA         | NA        | NA         | OFF             | NA            | 3.3       
sw2             |           | 3/3           | Y          | in    | IOT2[A]  | LVCMOS18   | NA    | UP        | ON        | NONE       | NA         | NA        | NA         | OFF             | NA            | 1.8       
rotary1_a       |           | 41/2          | Y          | in    | IOB41[A] | LVCMOS33   | NA    | UP        | ON        | NONE       | NA         | NA        | NA         | NA              | NA            | 3.3       
rotary1_b       |           | 42/2          | Y          | in    | IOB41[B] | LVCMOS33   | NA    | UP        | ON        | NONE       | NA         | NA        | NA         | NA              | NA            | 3.3       
rotary1_SW      |           | 63/1          | Y          | in    | IOR5[A]  | LVCMOS33   | NA    | UP        | ON        | NONE       | NA         | NA        | NA         | OFF             | NA            | 3.3       
ch1_phase_a     |           | 25/2          | Y          | out   | IOB8[A]  | LVCMOS33   | 8     | UP        | NA        | NA         | OFF        | FAST      | NA         | NA              | NA            | 3.3       
ch1_phase_b     |           | 39/2          | Y          | out   | IOB33[A] | LVCMOS33   | 8     | UP        | NA        | NA         | OFF        | FAST      | NA         | NA              | NA            | 3.3       
ch1_INB1        |           | 36/2          | Y          | out   | IOB29[B] | LVCMOS33   | 8     | UP        | NA        | NA         | OFF        | FAST      | NA         | NA              | NA            | 3.3       
ch1_INB2        |           | 37/2          | Y          | out   | IOB31[A] | LVCMOS33   | 8     | UP        | NA        | NA         | OFF        | FAST      | NA         | NA              | NA            | 3.3       
ch1_INA1        |           | 30/2          | Y          | out   | IOB13[B] | LVCMOS33   | 8     | UP        | NA        | NA         | OFF        | FAST      | NA         | NA              | NA            | 3.3       
ch1_INA2        |           | 26/2          | Y          | out   | IOB8[B]  | LVCMOS33   | 8     | UP        | NA        | NA         | OFF        | FAST      | NA         | NA              | NA            | 3.3       
ch1_STANBY      |           | 38/2          | Y          | out   | IOB31[B] | LVCMOS33   | 8     | UP        | NA        | NA         | OFF        | FAST      | NA         | NA              | NA            | 3.3       
ch1_VREF        |           | 27/2          | Y          | out   | IOB11[A] | LVCMOS33   | 8     | UP        | NA        | NA         | OFF        | FAST      | NA         | NA              | NA            | 3.3       
boardLED[0]     |           | 10/3          | Y          | out   | IOL15[A] | LVCMOS18   | 8     | UP        | NA        | NA         | OFF        | FAST      | NA         | OFF             | NA            | 1.8       
boardLED[1]     |           | 11/3          | Y          | out   | IOL16[B] | LVCMOS18   | 8     | UP        | NA        | NA         | OFF        | FAST      | NA         | OFF             | NA            | 1.8       
boardLED[2]     |           | 13/3          | Y          | out   | IOL21[B] | LVCMOS18   | 8     | UP        | NA        | NA         | OFF        | FAST      | NA         | OFF             | NA            | 1.8       
boardLED[3]     |           | 14/3          | Y          | out   | IOL22[B] | LVCMOS18   | 8     | UP        | NA        | NA         | OFF        | FAST      | NA         | OFF             | NA            | 1.8       
boardLED[4]     |           | 15/3          | Y          | out   | IOL25[B] | LVCMOS18   | 8     | UP        | NA        | NA         | OFF        | FAST      | NA         | OFF             | NA            | 1.8       
boardLED[5]     |           | 16/3          | Y          | out   | IOL26[B] | LVCMOS18   | 8     | UP        | NA        | NA         | OFF        | FAST      | NA         | OFF             | NA            | 1.8       
tmds_clk_p      |           | 69/1          | Y          | out   | IOT42[A] | LVCMOS33D  | 8     | NONE      | NA        | NA         | NA         | FAST      | NA         | OFF             | NA            | 3.3       
tmds_data_p[0]  |           | 71/1          | Y          | out   | IOT41[A] | LVCMOS33D  | 8     | NONE      | NA        | NA         | NA         | FAST      | NA         | OFF             | NA            | 3.3       
tmds_data_p[1]  |           | 73/1          | Y          | out   | IOT39[A] | LVCMOS33D  | 8     | NONE      | NA        | NA         | NA         | FAST      | NA         | OFF             | NA            | 3.3       
tmds_data_p[2]  |           | 75/1          | Y          | out   | IOT38[A] | LVCMOS33D  | 8     | NONE      | NA        | NA         | NA         | FAST      | NA         | OFF             | NA            | 3.3       
scl             |           | 28/2          | Y          | io    | IOB11[B] | LVCMOS33   | 8     | UP        | NA        | NONE       | ON         | FAST      | NA         | NA              | NA            | 3.3       
sda             |           | 29/2          | Y          | io    | IOB13[A] | LVCMOS33   | 8     | UP        | NA        | NONE       | ON         | FAST      | NA         | NA              | NA            | 3.3       
=======================================================================================================================================================================================================================

8. All Package Pins

--------------------------------------------------------------------------------------------------------------------------------------------------------------------------------------------
Loc./Bank| Signal          | Dir.  | Site     | IO Type  | Drive | Pull Mode | PCI Clamp | Hysteresis | Open Drain | Slew Rate | Vref       | Single Resistor | Diff Resistor | Bank Vccio
--------------------------------------------------------------------------------------------------------------------------------------------------------------------------------------------
3/3      | sw2             | in    | IOT2[A]  | LVCMOS18 | NA    | UP        | ON        | NONE       | NA         | NA        | NA         | OFF             | NA            | 1.8  
88/3     | -               | in    | IOT5[A]  | LVCMOS18 | NA    | UP        | ON        | NONE       | NA         | NA        | NA         | NA              | NA            | 1.8  
87/3     | -               | in    | IOT6[B]  | LVCMOS18 | NA    | UP        | ON        | NONE       | NA         | NA        | NA         | NA              | NA            | 1.8  
86/3     | -               | in    | IOT8[A]  | LVCMOS18 | NA    | UP        | ON        | NONE       | NA         | NA        | NA         | NA              | NA            | 1.8  
85/3     | -               | in    | IOT8[B]  | LVCMOS18 | NA    | UP        | ON        | NONE       | NA         | NA        | NA         | NA              | NA            | 1.8  
84/3     | -               | in    | IOT10[A] | LVCMOS18 | NA    | UP        | ON        | NONE       | NA         | NA        | NA         | NA              | NA            | 1.8  
83/3     | -               | in    | IOT10[B] | LVCMOS18 | NA    | UP        | ON        | NONE       | NA         | NA        | NA         | NA              | NA            | 1.8  
82/3     | -               | in    | IOT11[A] | LVCMOS18 | NA    | UP        | ON        | NONE       | NA         | NA        | NA         | NA              | NA            | 1.8  
81/3     | -               | in    | IOT11[B] | LVCMOS18 | NA    | UP        | ON        | NONE       | NA         | NA        | NA         | NA              | NA            | 1.8  
80/3     | -               | in    | IOT12[A] | LVCMOS18 | NA    | UP        | ON        | NONE       | NA         | NA        | NA         | NA              | NA            | 1.8  
79/3     | -               | in    | IOT12[B] | LVCMOS18 | NA    | UP        | ON        | NONE       | NA         | NA        | NA         | NA              | NA            | 1.8  
77/1     | -               | in    | IOT37[A] | LVCMOS18 | NA    | UP        | ON        | NONE       | NA         | NA        | NA         | NA              | NA            | 3.3  
76/1     | -               | in    | IOT37[B] | LVCMOS18 | NA    | UP        | ON        | NONE       | NA         | NA        | NA         | NA              | NA            | 3.3  
75/1     | tmds_data_p[2](p) | out   | IOT38[A] | LVCMOS33D | 8     | NONE      | NA        | NA         | NA         | FAST      | NA         | OFF             | NA            | 3.3  
74/1     | tmds_data_p[2](n) | out   | IOT38[B] | LVCMOS33D | 8     | NONE      | NA        | NA         | NA         | FAST      | NA         | OFF             | NA            | 3.3  
73/1     | tmds_data_p[1](p) | out   | IOT39[A] | LVCMOS33D | 8     | NONE      | NA        | NA         | NA         | FAST      | NA         | OFF             | NA            | 3.3  
72/1     | tmds_data_p[1](n) | out   | IOT39[B] | LVCMOS33D | 8     | NONE      | NA        | NA         | NA         | FAST      | NA         | OFF             | NA            | 3.3  
71/1     | tmds_data_p[0](p) | out   | IOT41[A] | LVCMOS33D | 8     | NONE      | NA        | NA         | NA         | FAST      | NA         | OFF             | NA            | 3.3  
70/1     | tmds_data_p[0](n) | out   | IOT41[B] | LVCMOS33D | 8     | NONE      | NA        | NA         | NA         | FAST      | NA         | OFF             | NA            | 3.3  
69/1     | tmds_clk_p(p)   | out   | IOT42[A] | LVCMOS33D | 8     | NONE      | NA        | NA         | NA         | FAST      | NA         | OFF             | NA            | 3.3  
68/1     | tmds_clk_p(n)   | out   | IOT42[B] | LVCMOS33D | 8     | NONE      | NA        | NA         | NA         | FAST      | NA         | OFF             | NA            | 3.3  
--------------------------------------------------------------------------------------------------------------------------------------------------------------------------------------------
17/2     | -               | in    | IOB2[A]  | LVCMOS18 | NA    | UP        | ON        | NONE       | NA         | NA        | NA         | NA              | NA            | 3.3  
18/2     | -               | in    | IOB2[B]  | LVCMOS18 | NA    | UP        | ON        | NONE       | NA         | NA        | NA         | NA              | NA            | 3.3  
19/2     | -               | in    | IOB4[A]  | LVCMOS18 | NA    | UP        | ON        | NONE       | NA         | NA        | NA         | NA              | NA            | 3.3  
20/2     | -               | in    | IOB4[B]  | LVCMOS18 | NA    | UP        | ON        | NONE       | NA         | NA        | NA         | NA              | NA            | 3.3  
25/2     | ch1_phase_a     | out   | IOB8[A]  | LVCMOS33 | 8     | UP        | NA        | NA         | OFF        | FAST      | NA         | NA              | NA            | 3.3  
26/2     | ch1_INA2        | out   | IOB8[B]  | LVCMOS33 | 8     | UP        | NA        | NA         | OFF        | FAST      | NA         | NA              | NA            | 3.3  
27/2     | ch1_VREF        | out   | IOB11[A] | LVCMOS33 | 8     | UP        | NA        | NA         | OFF        | FAST      | NA         | NA              | NA            | 3.3  
28/2     | scl             | io    | IOB11[B] | LVCMOS33 | 8     | UP        | NA        | NONE       | ON         | FAST      | NA         | NA              | NA            | 3.3  
29/2     | sda             | io    | IOB13[A] | LVCMOS33 | 8     | UP        | NA        | NONE       | ON         | FAST      | NA         | NA              | NA            | 3.3  
30/2     | ch1_INA1        | out   | IOB13[B] | LVCMOS33 | 8     | UP        | NA        | NA         | OFF        | FAST      | NA         | NA              | NA            | 3.3  
31/2     | -               | in    | IOB15[A] | LVCMOS18 | NA    | UP        | ON        | NONE       | NA         | NA        | NA         | NA              | NA            | 3.3  
32/2     | -               | in    | IOB15[B] | LVCMOS18 | NA    | UP        | ON        | NONE       | NA         | NA        | NA         | NA              | NA            | 3.3  
33/2     | -               | in    | IOB23[A] | LVCMOS18 | NA    | UP        | ON        | NONE       | NA         | NA        | NA         | NA              | NA            | 3.3  
34/2     | -               | in    | IOB23[B] | LVCMOS18 | NA    | UP        | ON        | NONE       | NA         | NA        | NA         | NA              | NA            | 3.3  
35/2     | -               | in    | IOB29[A] | LVCMOS18 | NA    | UP        | ON        | NONE       | NA         | NA        | NA         | NA              | NA            | 3.3  
36/2     | ch1_INB1        | out   | IOB29[B] | LVCMOS33 | 8     | UP        | NA        | NA         | OFF        | FAST      | NA         | NA              | NA            | 3.3  
37/2     | ch1_INB2        | out   | IOB31[A] | LVCMOS33 | 8     | UP        | NA        | NA         | OFF        | FAST      | NA         | NA              | NA            | 3.3  
38/2     | ch1_STANBY      | out   | IOB31[B] | LVCMOS33 | 8     | UP        | NA        | NA         | OFF        | FAST      | NA         | NA              | NA            | 3.3  
39/2     | ch1_phase_b     | out   | IOB33[A] | LVCMOS33 | 8     | UP        | NA        | NA         | OFF        | FAST      | NA         | NA              | NA            | 3.3  
40/2     | -               | in    | IOB33[B] | LVCMOS18 | NA    | UP        | ON        | NONE       | NA         | NA        | NA         | NA              | NA            | 3.3  
41/2     | rotary1_a       | in    | IOB41[A] | LVCMOS33 | NA    | UP        | ON        | NONE       | NA         | NA        | NA         | NA              | NA            | 3.3  
42/2     | rotary1_b       | in    | IOB41[B] | LVCMOS33 | NA    | UP        | ON        | NONE       | NA         | NA        | NA         | NA              | NA            | 3.3  
47/2     | -               | in    | IOB43[B] | LVCMOS18 | NA    | UP        | ON        | NONE       | NA         | NA        | NA         | NA              | NA            | 3.3  
--------------------------------------------------------------------------------------------------------------------------------------------------------------------------------------------
4/3      | -               | in    | IOL5[A]  | LVCMOS18 | NA    | UP        | ON        | NONE       | NA         | NA        | NA         | NA              | NA            | 1.8  
5/3      | -               | in    | IOL11[A] | LVCMOS18 | NA    | UP        | ON        | NONE       | NA         | NA        | NA         | NA              | NA            | 1.8  
6/3      | -               | in    | IOL11[B] | LVCMOS18 | NA    | UP        | ON        | NONE       | NA         | NA        | NA         | NA              | NA            | 1.8  
7/3      | -               | in    | IOL12[B] | LVCMOS18 | NA    | UP        | ON        | NONE       | NA         | NA        | NA         | NA              | NA            | 1.8  
8/3      | -               | out   | IOL13[A] | LVCMOS18 | 8     | UP        | NA        | NA         | OFF        | FAST      | NA         | NA              | NA            | 1.8  
9/3      | -               | in    | IOL13[B] | LVCMOS18 | NA    | UP        | ON        | NONE       | NA         | NA        | NA         | NA              | NA            | 1.8  
10/3     | boardLED[0]     | out   | IOL15[A] | LVCMOS18 | 8     | UP        | NA        | NA         | OFF        | FAST      | NA         | OFF             | NA            | 1.8  
11/3     | boardLED[1]     | out   | IOL16[B] | LVCMOS18 | 8     | UP        | NA        | NA         | OFF        | FAST      | NA         | OFF             | NA            | 1.8  
13/3     | boardLED[2]     | out   | IOL21[B] | LVCMOS18 | 8     | UP        | NA        | NA         | OFF        | FAST      | NA         | OFF             | NA            | 1.8  
14/3     | boardLED[3]     | out   | IOL22[B] | LVCMOS18 | 8     | UP        | NA        | NA         | OFF        | FAST      | NA         | OFF             | NA            | 1.8  
15/3     | boardLED[4]     | out   | IOL25[B] | LVCMOS18 | 8     | UP        | NA        | NA         | OFF        | FAST      | NA         | OFF             | NA            | 1.8  
16/3     | boardLED[5]     | out   | IOL26[B] | LVCMOS18 | 8     | UP        | NA        | NA         | OFF        | FAST      | NA         | OFF             | NA            | 1.8  
--------------------------------------------------------------------------------------------------------------------------------------------------------------------------------------------
63/1     | rotary1_SW      | in    | IOR5[A]  | LVCMOS33 | NA    | UP        | ON        | NONE       | NA         | NA        | NA         | OFF             | NA            | 3.3  
62/1     | -               | in    | IOR11[A] | LVCMOS18 | NA    | UP        | ON        | NONE       | NA         | NA        | NA         | NA              | NA            | 3.3  
61/1     | -               | in    | IOR11[B] | LVCMOS18 | NA    | UP        | ON        | NONE       | NA         | NA        | NA         | NA              | NA            | 3.3  
60/1     | -               | in    | IOR12[A] | LVCMOS18 | NA    | UP        | ON        | NONE       | NA         | NA        | NA         | NA              | NA            | 3.3  
59/1     | -               | in    | IOR12[B] | LVCMOS18 | NA    | UP        | ON        | NONE       | NA         | NA        | NA         | NA              | NA            | 3.3  
57/1     | -               | in    | IOR13[A] | LVCMOS18 | NA    | UP        | ON        | NONE       | NA         | NA        | NA         | NA              | NA            | 3.3  
56/1     | -               | in    | IOR14[A] | LVCMOS18 | NA    | UP        | ON        | NONE       | NA         | NA        | NA         | NA              | NA            | 3.3  
55/1     | -               | in    | IOR14[B] | LVCMOS18 | NA    | UP        | ON        | NONE       | NA         | NA        | NA         | NA              | NA            | 3.3  
54/1     | -               | in    | IOR15[A] | LVCMOS18 | NA    | UP        | ON        | NONE       | NA         | NA        | NA         | NA              | NA            | 3.3  
53/1     | -               | in    | IOR15[B] | LVCMOS18 | NA    | UP        | ON        | NONE       | NA         | NA        | NA         | NA              | NA            | 3.3  
52/1     | clk             | in    | IOR17[A] | LVCMOS33 | NA    | UP        | ON        | NONE       | NA         | NA        | NA         | OFF             | NA            | 3.3  
51/1     | -               | in    | IOR17[B] | LVCMOS18 | NA    | UP        | ON        | NONE       | NA         | NA        | NA         | NA              | NA            | 3.3  
50/1     | -               | in    | IOR22[B] | LVCMOS18 | NA    | UP        | ON        | NONE       | NA         | NA        | NA         | NA              | NA            | 3.3  
49/1     | -               | in    | IOR24[A] | LVCMOS18 | NA    | UP        | ON        | NONE       | NA         | NA        | NA         | NA              | NA            | 3.3  
48/1     | -               | in    | IOR24[B] | LVCMOS18 | NA    | UP        | ON        | NONE       | NA         | NA        | NA         | NA              | NA            | 3.3  
--------------------------------------------------------------------------------------------------------------------------------------------------------------------------------------------
============================================================================================================================================================================================

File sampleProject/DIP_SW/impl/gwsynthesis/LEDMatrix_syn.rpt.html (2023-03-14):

- Synthesis Messages
- Synthesis Details
- Resource
  - Resource Usage Summary
  - Resource Utilization Summary

# Synthesis Messages

Report Title | GowinSynthesis Report
Design File | E:\git\TangNano9K_motordriver\sampleProject\Polyphony_DIP_SW\src\LEDMatrixAB_m.v E:\git\TangNano9K_motordriver\sampleProject\Polyphony_DIP_SW\src\top.sv
GowinSynthesis Constraints File | ---
Version | GowinSynthesis V1.9.8.09 Education
Part Number | GW1NR-LV9QN88PC6/I5
Device | GW1NR-9C
Created Time | Tue Mar 14 19:40:47 2023
Legal Announcement | Copyright (C)2014-2022 Gowin Semiconductor Corporation. ALL rights reserved.

# Synthesis Details

Top Level Module | top

Synthesis Process

Running parser:
CPU time = 0h 0m 0.062s, Elapsed time = 0h 0m 0.087s, Peak memory usage = 181.207MB
Running netlist conversion:
CPU time = 0h 0m 0s, Elapsed time = 0h 0m 0s, Peak memory usage = 0MB
Running device independent optimization:
Optimizing Phase 0: CPU time = 0h 0m 0s, Elapsed time = 0h 0m 0s, Peak memory usage = 181.207MB
Optimizing Phase 1: CPU time = 0h 0m 0s, Elapsed time = 0h 0m 0s, Peak memory usage = 181.207MB
Optimizing Phase 2: CPU time = 0h 0m 0.015s, Elapsed time = 0h 0m 0s, Peak memory usage = 181.207MB
Running inference:
Inferring Phase 0: CPU time = 0h 0m 0s, Elapsed time = 0h 0m 0s, Peak memory usage = 181.207MB
Inferring Phase 1: CPU time = 0h 0m 0s, Elapsed time = 0h 0m 0s, Peak memory usage = 181.207MB
Inferring Phase 2: CPU time = 0h 0m 0s, Elapsed time = 0h 0m 0s, Peak memory usage = 181.207MB
Inferring Phase 3: CPU time = 0h 0m 0s, Elapsed time = 0h 0m 0s, Peak memory usage = 181.207MB
Running technical mapping:
Tech-Mapping Phase 0: CPU time = 0h 0m 0s, Elapsed time = 0h 0m 0s, Peak memory usage = 181.207MB
Tech-Mapping Phase 1: CPU time = 0h 0m 0s, Elapsed time = 0h 0m 0s, Peak memory usage = 181.207MB
Tech-Mapping Phase 2: CPU time = 0h 0m 0s, Elapsed time = 0h 0m 0s, Peak memory usage = 181.207MB
Tech-Mapping Phase 3: CPU time = 0h 0m 0.015s, Elapsed time = 0h 0m 0.03s, Peak memory usage = 181.207MB
Tech-Mapping Phase 4: CPU time = 0h 0m 0s, Elapsed time = 0h 0m 0s, Peak memory usage = 181.207MB
Generate output files:
CPU time = 0h 0m 0.015s, Elapsed time = 0h 0m 0.001s, Peak memory usage = 181.207MB
Total Time and Memory Usage | CPU time = 0h 0m 0.107s, Elapsed time = 0h 0m 0.118s, Peak memory usage = 181.207MB

# Resource

## Resource Usage Summary

Resource | Usage
I/O Port | 34
I/O Buf | 25
IBUF | 8
OBUF | 16
TBUF | 1

## Resource Utilization Summary

Resource | Usage | Utilization
Logic | 0(0 LUTs, 0 ALUs) / 8640 | 0%
Register | 0 / 6693 | 0%
--Register as Latch | 0 / 6693 | 0%
--Register as FF | 0 / 6693 | 0%
BSRAM | 0 / 26 | 0%

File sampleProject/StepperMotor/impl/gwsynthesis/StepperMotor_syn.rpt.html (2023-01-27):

- Synthesis Messages
- Synthesis Details
- Resource
  - Resource Usage Summary
  - Resource Utilization Summary
- Timing
  - Clock Summary
  - Max Frequency Summary
  - Detail Timing Paths Informations

# Synthesis Messages

Report Title | GowinSynthesis Report

Design File

E:\git\TangNano9K_motordriver\sampleProject\StepperMotor\src\Motor_12.sv
E:\git\TangNano9K_motordriver\sampleProject\StepperMotor\src\Motor_2.sv
E:\git\TangNano9K_motordriver\sampleProject\StepperMotor\src\Motor_w12.sv
E:\git\TangNano9K_motordriver\sampleProject\StepperMotor\src\diagram_generator.sv
E:\git\TangNano9K_motordriver\sampleProject\StepperMotor\src\if202212_gowin-main\dvi_out_tpg\src\tangnano9k\ip\gowin_rpll\gowin_rpll.v
E:\git\TangNano9K_motordriver\sampleProject\StepperMotor\src\if202212_gowin-main\dvi_out_tpg\src\tangnano9k\ip\gowin_rpll_ser\gowin_rpll_ser.v
E:\git\TangNano9K_motordriver\sampleProject\StepperMotor\src\if202212_gowin-main\dvi_out_tpg\src\tangnano9k\reset_seq.sv
E:\git\TangNano9K_motordriver\sampleProject\StepperMotor\src\if202212_gowin-main\rtl\dvi_out\dvi_out.sv
E:\git\TangNano9K_motordriver\sampleProject\StepperMotor\src\top_w12.sv
GowinSynthesis Constraints File | ---
Version | GowinSynthesis V1.9.8.09 Education
Part Number | GW1NR-LV9QN88PC6/I5
Device | GW1NR-9C
Created Time | Thu Jan 26 13:42:40 2023
Legal Announcement | Copyright (C)2014-2022 Gowin Semiconductor Corporation. ALL rights reserved.

# Synthesis Details

Top Level Module | top_w12

Synthesis Process

Running parser:
CPU time = 0h 0m 0.171s, Elapsed time = 0h 0m 0.176s, Peak memory usage = 192.004MB
Running netlist conversion:
CPU time = 0h 0m 0s, Elapsed time = 0h 0m 0s, Peak memory usage = 0MB
Running device independent optimization:
Optimizing Phase 0: CPU time = 0h 0m 0.015s, Elapsed time = 0h 0m 0.032s, Peak memory usage = 192.004MB
Optimizing Phase 1: CPU time = 0h 0m 0.015s, Elapsed time = 0h 0m 0.012s, Peak memory usage = 192.004MB
Optimizing Phase 2: CPU time = 0h 0m 0.046s, Elapsed time = 0h 0m 0.046s, Peak memory usage = 192.004MB
Running inference:
Inferring Phase 0: CPU time = 0h 0m 0s, Elapsed time = 0h 0m 0.011s, Peak memory usage = 192.004MB
Inferring Phase 1: CPU time = 0h 0m 0.015s, Elapsed time = 0h 0m 0.007s, Peak memory usage = 192.004MB
Inferring Phase 2: CPU time = 0h 0m 0s, Elapsed time = 0h 0m 0.002s, Peak memory usage = 192.004MB
Inferring Phase 3: CPU time = 0h 0m 0s, Elapsed time = 0h 0m 0.004s, Peak memory usage = 192.004MB
Running technical mapping:
Tech-Mapping Phase 0: CPU time = 0h 0m 0.031s, Elapsed time = 0h 0m 0.04s, Peak memory usage = 192.004MB
Tech-Mapping Phase 1: CPU time = 0h 0m 0.015s, Elapsed time = 0h 0m 0.007s, Peak memory usage = 192.004MB
Tech-Mapping Phase 2: CPU time = 0h 0m 0s, Elapsed time = 0h 0m 0.009s, Peak memory usage = 192.004MB
Tech-Mapping Phase 3: CPU time = 0h 0m 3s, Elapsed time = 0h 0m 3s, Peak memory usage = 192.004MB
Tech-Mapping Phase 4: CPU time = 0h 0m 0.046s, Elapsed time = 0h 0m 0.061s, Peak memory usage = 192.004MB
Generate output files:
CPU time = 0h 0m 0.015s, Elapsed time = 0h 0m 0.026s, Peak memory usage = 192.004MB
Total Time and Memory Usage | CPU time = 0h 0m 3s, Elapsed time = 0h 0m 3s, Peak memory usage = 192.004MB

# Resource

## Resource Usage Summary

Resource | Usage
I/O Port | 25
I/O Buf | 22
IBUF | 4
OBUF | 18
Register | 183
DFF | 20
DFFE | 12
DFFS | 28
DFFSE | 1
DFFR | 105
DFFRE | 17
LUT | 434
LUT2 | 72
LUT3 | 139
LUT4 | 223
ALU | 103
ALU | 103
INV | 14
INV | 14
IOLOGIC | 4
OSER10 | 4
CLOCK | 2
rPLL | 2

## Resource Utilization Summary

Resource | Usage | Utilization
Logic | 551(448 LUTs, 103 ALUs) / 8640 | 6%
Register | 183 / 6693 | 3%
--Register as Latch | 0 / 6693 | 0%
--Register as FF | 183 / 6693 | 3%
BSRAM | 0 / 26 | 0%

# Timing

## Clock Summary:

Clock Name | Type | Period | Frequency(MHz) | Rise | Fall | Source | Master | Object
clk | Base | 37.037 | 27.0 | 0.000 | 18.519 | | | clk_ibuf/I
motor_pulse_4 | Base | 20.000 | 50.0 | 0.000 | 10.000 | | | motor_pulse_s1/Q
rpll_dvi/rpll_inst/CLKOUT.default_gen_clk | Generated | 13.468 | 74.3 | 0.000 | 6.734 | clk_ibuf/I | clk | rpll_dvi/rpll_inst/CLKOUT
rpll_dvi/rpll_inst/CLKOUTP.default_gen_clk | Generated | 13.468 | 74.3 | 0.000 | 6.734 | clk_ibuf/I | clk | rpll_dvi/rpll_inst/CLKOUTP
rpll_dvi/rpll_inst/CLKOUTD.default_gen_clk | Generated | 26.936 | 37.1 | 0.000 | 13.468 | clk_ibuf/I | clk | rpll_dvi/rpll_inst/CLKOUTD
rpll_dvi/rpll_inst/CLKOUTD3.default_gen_clk | Generated | 40.404 | 24.8 | 0.000 | 20.202 | clk_ibuf/I | clk | rpll_dvi/rpll_inst/CLKOUTD3
rpll_dvi_ser/rpll_inst/CLKOUT.default_gen_clk | Generated | 2.694 | 371.3 | 0.000 | 1.347 | rpll_dvi/rpll_inst/CLKOUT | rpll_dvi/rpll_inst/CLKOUT.default_gen_clk | rpll_dvi_ser/rpll_inst/CLKOUT
rpll_dvi_ser/rpll_inst/CLKOUTP.default_gen_clk | Generated | 2.694 | 371.3 | 0.000 | 1.347 | rpll_dvi/rpll_inst/CLKOUT | rpll_dvi/rpll_inst/CLKOUT.default_gen_clk | rpll_dvi_ser/rpll_inst/CLKOUTP
rpll_dvi_ser/rpll_inst/CLKOUTD.default_gen_clk | Generated | 5.387 | 185.6 | 0.000 | 2.694 | rpll_dvi/rpll_inst/CLKOUT | rpll_dvi/rpll_inst/CLKOUT.default_gen_clk | rpll_dvi_ser/rpll_inst/CLKOUTD
rpll_dvi_ser/rpll_inst/CLKOUTD3.default_gen_clk | Generated | 8.081 | 123.7 | 0.000 | 4.040 | rpll_dvi/rpll_inst/CLKOUT | rpll_dvi/rpll_inst/CLKOUT.default_gen_clk | rpll_dvi_ser/rpll_inst/CLKOUTD3

## Max Frequency Summary:

No. | Clock Name | Constraint | Actual Fmax | Logic Level | Entity
1 | clk | 27.0(MHz) | 178.5(MHz) | 4 | TOP
2 | motor_pulse_4 | 50.0(MHz) | 342.8(MHz) | 2 | TOP
3 | rpll_dvi/rpll_inst/CLKOUT.default_gen_clk | 74.3(MHz) | 58.6(MHz) | 11 | TOP

## Detail Timing Paths Information

### Path 1

Path Summary:

Slack | -4.316
Data Arrival Time | 745.971
Data Required Time | 741.656
From | inst_w12/phase_counter_1_s0
To | ch1_phase_b_s2
Launch Clk | motor_pulse_4[R]
Latch Clk | clk[R]

Data Arrival Path:

AT | DELAY | TYPE | RF | FANOUT | NODE
740.000 | 0.000 | | | | motor_pulse_4
740.000 | 0.000 | tCL | RR | 10 | motor_pulse_s1/Q
740.363 | 0.363 | tNET | RR | 1 | inst_w12/phase_counter_1_s0/CLK
740.821 | 0.458 | tC2Q | RF | 8 | inst_w12/phase_counter_1_s0/Q
741.301 | 0.480 | tNET | FF | 1 | inst_w12/n20_s0/I1
742.400 | 1.099 | tINS | FF | 2 | inst_w12/n20_s0/F
742.880 | 0.480 | tNET | FF | 1 | n166_s5/I0
743.912 | 1.032 | tINS | FF | 1 | n166_s5/F
744.392 | 0.480 | tNET | FF | 1 | n166_s4/I1
745.491 | 1.099 | tINS | FF | 1 | n166_s4/F
745.971 | 0.480 | tNET | FF | 1 | ch1_phase_b_s2/D

Data Required Path:

AT | DELAY | TYPE | RF | FANOUT | NODE
740.741 | 0.000 | | | | clk
740.741 | 0.000 | tCL | RR | 1 | clk_ibuf/I
741.723 | 0.982 | tINS | RR | 53 | clk_ibuf/O
742.086 | 0.363 | tNET | RR | 1 | ch1_phase_b_s2/CLK
742.056 | -0.030 | tUnc | | | ch1_phase_b_s2
741.656 | -0.400 | tSu | | 1 | ch1_phase_b_s2

Path Statistics:

Clock Skew: | 0.982
Setup Relationship: | 0.741
Logic Level: | 4
Arrival Clock Path Delay: | cell: 0.000, 0.000%; route: 0.363, 100.000%
Arrival Data Path Delay: | cell: 3.230, 57.593%; route: 1.920, 34.235%; tC2Q: 0.458, 8.172%
Required Clock Path Delay: | cell: 0.000, 0.000%; route: 0.363, 100.000%

### Path 2

Path Summary:

Slack | -4.249
Data Arrival Time | 745.904
Data Required Time | 741.656
From | inst_w12/phase_counter_1_s0
To | ch1_phase_a_s2
Launch Clk | motor_pulse_4[R]
Latch Clk | clk[R]

Data Arrival Path:

AT | DELAY | TYPE | RF | FANOUT | NODE
740.000 | 0.000 | | | | motor_pulse_4
740.000 | 0.000 | tCL | RR | 10 | motor_pulse_s1/Q
740.363 | 0.363 | tNET | RR | 1 | inst_w12/phase_counter_1_s0/CLK
740.821 | 0.458 | tC2Q | RF | 8 | inst_w12/phase_counter_1_s0/Q
741.301 | 0.480 | tNET | FF | 1 | n165_s6/I1
742.400 | 1.099 | tINS | FF | 1 | n165_s6/F
742.880 | 0.480 | tNET | FF | 1 | n165_s5/I0
743.912 | 1.032 | tINS | FF | 1 | n165_s5/F
744.392 | 0.480 | tNET | FF | 1 | n165_s7/I0
745.424 | 1.032 | tINS | FF | 1 | n165_s7/F
745.904 | 0.480 | tNET | FF | 1 | ch1_phase_a_s2/D

Data Required Path:

AT | DELAY | TYPE | RF | FANOUT | NODE
740.741 | 0.000 | | | | clk
740.741 | 0.000 | tCL | RR | 1 | clk_ibuf/I
741.723 | 0.982 | tINS | RR | 53 | clk_ibuf/O
742.086 | 0.363 | tNET | RR | 1 | ch1_phase_a_s2/CLK
742.056 | -0.030 | tUnc | | | ch1_phase_a_s2
741.656 | -0.400 | tSu | | 1 | ch1_phase_a_s2

Path Statistics:

Clock Skew: | 0.982
Setup Relationship: | 0.741
Logic Level: | 4
Arrival Clock Path Delay: | cell: 0.000, 0.000%; route: 0.363, 100.000%
Arrival Data Path Delay: | cell: 3.163, 57.080%; route: 1.920, 34.649%; tC2Q: 0.458, 8.271%
Required Clock Path Delay: | cell: 0.000, 0.000%; route: 0.363, 100.000%

### Path 3

Path Summary:

Slack | -3.593
Data Arrival Time | 18.782
Data Required Time | 15.189
From | tpg_inst/hcounter_6_s0
To | tpg_inst/video_data_22_s0
Launch Clk | rpll_dvi/rpll_inst/CLKOUT.default_gen_clk[R]
Latch Clk | rpll_dvi/rpll_inst/CLKOUT.default_gen_clk[R]

Data Arrival Path:

AT | DELAY | TYPE | RF | FANOUT | NODE
0.000 | 0.000 | | | | rpll_dvi/rpll_inst/CLKOUT.default_gen_clk
1.758 | 1.758 | tCL | RR | 127 | rpll_dvi/rpll_inst/CLKOUT
2.121 | 0.363 | tNET | RR | 1 | tpg_inst/hcounter_6_s0/CLK
2.579 | 0.458 | tC2Q | RF | 9 | tpg_inst/hcounter_6_s0/Q
3.059 | 0.480 | tNET | FF | 1 | tpg_inst/n888_s111/I1
4.158 | 1.099 | tINS | FF | 2 | tpg_inst/n888_s111/F
4.638 | 0.480 | tNET | FF | 1 | tpg_inst/n888_s98/I1
5.737 | 1.099 | tINS | FF | 5 | tpg_inst/n888_s98/F
6.217 | 0.480 | tNET | FF | 1 | tpg_inst/n888_s70/I1
7.316 | 1.099 | tINS | FF | 10 | tpg_inst/n888_s70/F
7.796 | 0.480 | tNET | FF | 1 | tpg_inst/n888_s35/I1
8.895 | 1.099 | tINS | FF | 9 | tpg_inst/n888_s35/F
9.375 | 0.480 | tNET | FF | 1 | tpg_inst/n888_s86/I1
10.474 | 1.099 | tINS | FF | 1 | tpg_inst/n888_s86/F
10.954 | 0.480 | tNET | FF | 1 | tpg_inst/n888_s56/I1
12.053 | 1.099 | tINS | FF | 1 | tpg_inst/n888_s56/F
12.533 | 0.480 | tNET | FF | 1 | tpg_inst/n888_s25/I0
13.565 | 1.032 | tINS | FF | 1 | tpg_inst/n888_s25/F
14.045 | 0.480 | tNET | FF | 1 | tpg_inst/n888_s8/I1
15.144 | 1.099 | tINS | FF | 1 | tpg_inst/n888_s8/F
15.624 | 0.480 | tNET | FF | 1 | tpg_inst/n888_s2/I1
16.723 | 1.099 | tINS | FF | 2 | tpg_inst/n888_s2/F
17.203 | 0.480 | tNET | FF | 1 | tpg_inst/n1180_s0/I1
18.302 | 1.099 | tINS | FF | 1 | tpg_inst/n1180_s0/F
18.782 | 0.480 | tNET | FF | 1 | tpg_inst/video_data_22_s0/D

Data Required Path:

AT | DELAY | TYPE | RF | FANOUT | NODE
13.468 | 0.000 | | | | rpll_dvi/rpll_inst/CLKOUT.default_gen_clk
15.226 | 1.758 | tCL | RR | 127 | rpll_dvi/rpll_inst/CLKOUT
15.589 | 0.363 | tNET | RR | 1 | tpg_inst/video_data_22_s0/CLK
15.189 | -0.400 | tSu | | 1 | tpg_inst/video_data_22_s0

Path Statistics:

Clock Skew: | 0.000
Setup Relationship: | 13.468
Logic Level: | 11
Arrival Clock Path Delay: | cell: 0.000, 0.000%; route: 0.363, 100.000%
Arrival Data Path Delay: | cell: 10.923, 65.559%; route: 5.280, 31.690%; tC2Q: 0.458, 2.751%
Required Clock Path Delay: | cell: 0.000, 0.000%; route: 0.363, 100.000%

### Path 4

Path Summary:

Slack | -3.593
Data Arrival Time | 18.782
Data Required Time | 15.189
From | tpg_inst/hcounter_6_s0
To | tpg_inst/video_data_23_s0
Launch Clk | rpll_dvi/rpll_inst/CLKOUT.default_gen_clk[R]
Latch Clk | rpll_dvi/rpll_inst/CLKOUT.default_gen_clk[R]

Data Arrival Path:

AT | DELAY | TYPE | RF | FANOUT | NODE
0.000 | 0.000 | | | | rpll_dvi/rpll_inst/CLKOUT.default_gen_clk
1.758 | 1.758 | tCL | RR | 127 | rpll_dvi/rpll_inst/CLKOUT
2.121 | 0.363 | tNET | RR | 1 | tpg_inst/hcounter_6_s0/CLK
2.579 | 0.458 | tC2Q | RF | 9 | tpg_inst/hcounter_6_s0/Q
3.059 | 0.480 | tNET | FF | 1 | tpg_inst/n888_s111/I1
4.158 | 1.099 | tINS | FF | 2 | tpg_inst/n888_s111/F
4.638 | 0.480 | tNET | FF | 1 | tpg_inst/n888_s98/I1
5.737 | 1.099 | tINS | FF | 5 | tpg_inst/n888_s98/F
6.217 | 0.480 | tNET | FF | 1 | tpg_inst/n888_s70/I1
7.316 | 1.099 | tINS | FF | 10 | tpg_inst/n888_s70/F
7.796 | 0.480 | tNET | FF | 1 | tpg_inst/n888_s35/I1
8.895 | 1.099 | tINS | FF | 9 | tpg_inst/n888_s35/F
9.375 | 0.480 | tNET | FF | 1 | tpg_inst/n888_s86/I1
10.474 | 1.099 | tINS | FF | 1 | tpg_inst/n888_s86/F
10.954 | 0.480 | tNET | FF | 1 | tpg_inst/n888_s56/I1
12.053 | 1.099 | tINS | FF | 1 | tpg_inst/n888_s56/F
12.533 | 0.480 | tNET | FF | 1 | tpg_inst/n888_s25/I0
13.565 | 1.032 | tINS | FF | 1 | tpg_inst/n888_s25/F
14.045 | 0.480 | tNET | FF | 1 | tpg_inst/n888_s8/I1
15.144 | 1.099 | tINS | FF | 1 | tpg_inst/n888_s8/F
15.624 | 0.480 | tNET | FF | 1 | tpg_inst/n888_s2/I1
16.723 | 1.099 | tINS | FF | 2 | tpg_inst/n888_s2/F
17.203 | 0.480 | tNET | FF | 1 | tpg_inst/n1179_s0/I1
18.302 | 1.099 | tINS | FF | 1 | tpg_inst/n1179_s0/F
18.782 | 0.480 | tNET | FF | 1 | tpg_inst/video_data_23_s0/D

Data Required Path:

AT | DELAY | TYPE | RF | FANOUT | NODE
13.468 | 0.000 | | | | rpll_dvi/rpll_inst/CLKOUT.default_gen_clk
15.226 | 1.758 | tCL | RR | 127 | rpll_dvi/rpll_inst/CLKOUT
15.589 | 0.363 | tNET | RR | 1 | tpg_inst/video_data_23_s0/CLK
15.189 | -0.400 | tSu | | 1 | tpg_inst/video_data_23_s0

Path Statistics:

Clock Skew: | 0.000
Setup Relationship: | 13.468
Logic Level: | 11
Arrival Clock Path Delay: | cell: 0.000, 0.000%; route: 0.363, 100.000%
Arrival Data Path Delay: | cell: 10.923, 65.559%; route: 5.280, 31.690%; tC2Q: 0.458, 2.751%
Required Clock Path Delay: | cell: 0.000, 0.000%; route: 0.363, 100.000%

### Path 5

Path Summary:

Slack | -2.804
Data Arrival Time | 744.459
Data Required Time | 741.656
From | inst_w12/phase_counter_1_s0
To | ch1_INA1_s2
Launch Clk | motor_pulse_4[R]
Latch Clk | clk[R]

Data Arrival Path:

AT | DELAY | TYPE | RF | FANOUT | NODE
740.000 | 0.000 | | | | motor_pulse_4
740.000 | 0.000 | tCL | RR | 10 | motor_pulse_s1/Q
740.363 | 0.363 | tNET | RR | 1 | inst_w12/phase_counter_1_s0/CLK
740.821 | 0.458 | tC2Q | RF | 8 | inst_w12/phase_counter_1_s0/Q
741.301 | 0.480 | tNET | FF | 1 | inst_2/phase_counter_1_s4/I1
742.400 | 1.099 | tINS | FF | 2 | inst_2/phase_counter_1_s4/F
742.880 | 0.480 | tNET | FF | 1 | n169_s5/I1
743.979 | 1.099 | tINS | FF | 1 | n169_s5/F
744.459 | 0.480 | tNET | FF | 1 | ch1_INA1_s2/D

Data Required Path:

AT | DELAY | TYPE | RF | FANOUT | NODE
740.741 | 0.000 | | | | clk
740.741 | 0.000 | tCL | RR | 1 | clk_ibuf/I
741.723 | 0.982 | tINS | RR | 53 | clk_ibuf/O
742.086 | 0.363 | tNET | RR | 1 | ch1_INA1_s2/CLK
742.056 | -0.030 | tUnc | | | ch1_INA1_s2
741.656 | -0.400 | tSu | | 1 | ch1_INA1_s2

Path Statistics:

Clock Skew: | 0.982
Setup Relationship: | 0.741
Logic Level: | 3
Arrival Clock Path Delay: | cell: 0.000, 0.000%; route: 0.363, 100.000%
Arrival Data Path Delay: | cell: 2.198, 53.658%; route: 1.440, 35.153%; tC2Q: 0.458, 11.189%
Required Clock Path Delay: | cell: 0.000, 0.000%; route: 0.363, 100.000%

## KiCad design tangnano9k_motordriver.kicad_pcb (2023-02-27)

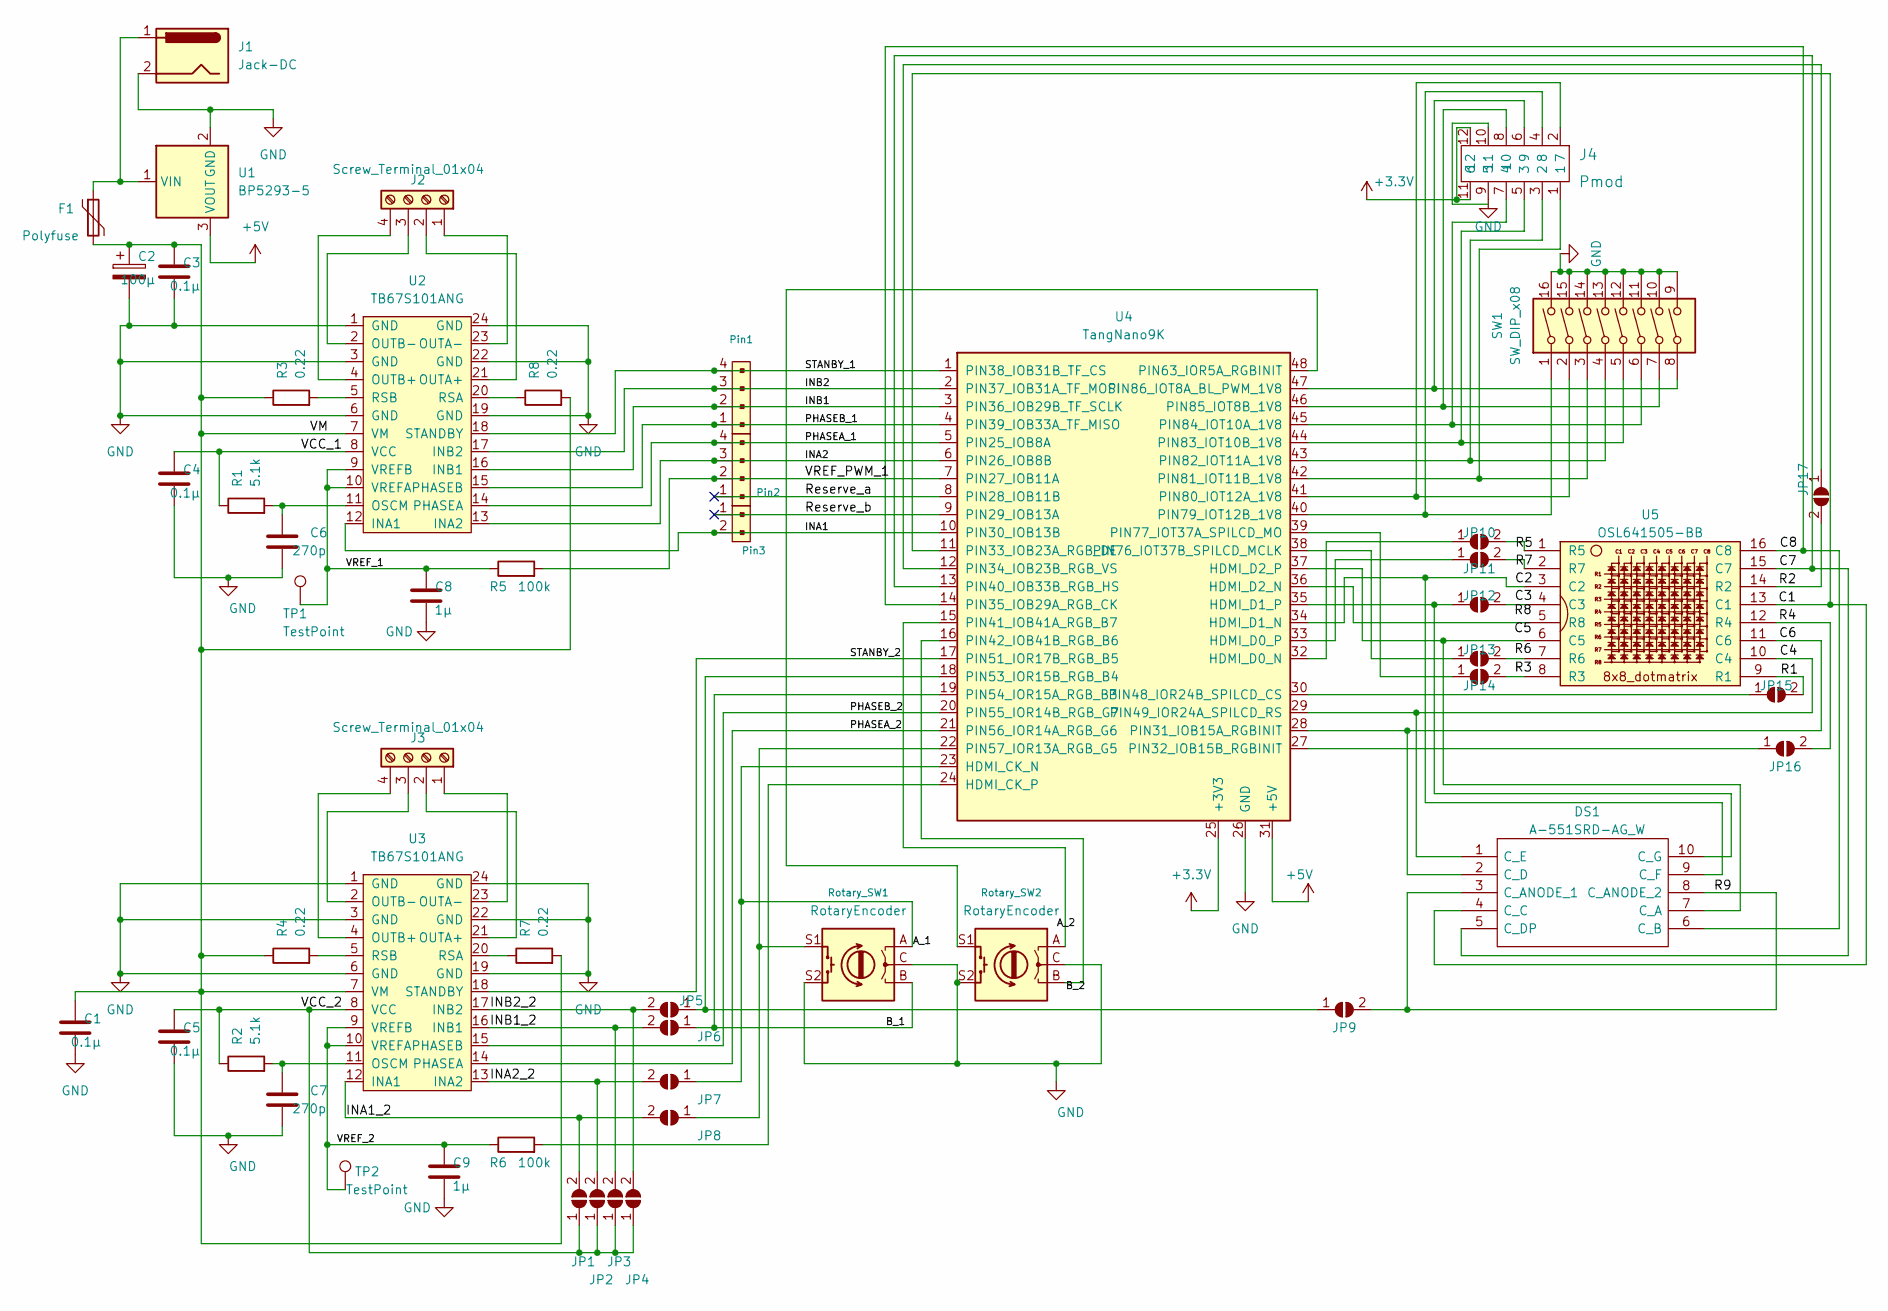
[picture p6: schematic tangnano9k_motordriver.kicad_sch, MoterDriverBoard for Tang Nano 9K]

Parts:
C1, C3, C4, C5: 0.1μ; C_Disc_D5.0mm_W2.5mm_P2.50mm
C2: 100μ; CP_Radial_D8.0mm_P2.50mm
C6, C7: 270p; C_Disc_D3.8mm_W2.6mm_P2.50mm
C8, C9: 1μ; C_Disc_D5.0mm_W2.5mm_P2.50mm
DS1: A-551SRD-AG_W; DIPS1524W51P254L1270H825Q10N; Manufacturer_Part_Number A-551SRD-AG/W
F1: Polyfuse; Fuse_Bourns_MF-RHT300
J1: Jack-DC; BarrelJack_Horizontal
J2, J3: Screw_Terminal_01x04; TerminalBlock_bornier-4_P5.08mm
J4: Pmod; PinSocket_2x06_P2.54mm_Horizontal; MPN 67996-412HLF; Digi-Key_PN 609-3219-ND
JP1, JP2, JP3, JP4, JP5, JP6, JP7, JP8, JP9: SolderJumper_2_Open; SolderJumper-2_P1.3mm_Open_TrianglePad1.0x1.5mm
JP10, JP11, JP12, JP13, JP14: SolderJumper_2_Open; SolderJumper_Register_Horizontal
JP15, JP16, JP17: SolderJumper_2_Open; SolderJumper_Register
Pin1, Pin2: Reserve; PinHeader_1x04_P2.54mm_Vertical
Pin3: Reserve; PinHeader_1x02_P2.54mm_Vertical
R1, R2: 5.1k; R_Axial_DIN0207_L6.3mm_D2.5mm_P7.62mm_Horizontal
R3, R4, R7, R8: 0.22; R_Axial_DIN0516_L15.5mm_D5.0mm_P20.32mm_Horizontal
R5, R6: 100k; R_Axial_DIN0207_L6.3mm_D2.5mm_P7.62mm_Horizontal
Rotary_SW1, Rotary_SW2: RotaryEncoder; RotaryEncoder_Alps_EC11E-Switch_Vertical_H20mm
SW1: SW_DIP_x08; SW_DIP_SPSTx08_Slide_9.78x22.5mm_W7.62mm_P2.54mm
TP1: TestPoint; TestPoint_THTPad_1.5x1.5mm_Drill0.7mm
TP2: TestPoint; TestPoint_Pad_1.5x1.5mm
U1: BP5293-5; PinHeader_1x03_P2.54mm_Vertical
U2, U3: TB67S101ANG
U4: TangNano9K; Tang_Nano_9K
U5: OSL641505-BB; OSL641501-ARA

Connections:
+3.3V: J4.11 (6), J4.12, U4.25 (+3V3)
+5V: U1.3 (VOUT), U4.31 (+5V)
/A_1: JP7.1 (A), Rotary_SW1.A, U4.23 (HDMI_CK_N)
/B_1: JP6.1 (A), Rotary_SW1.B, U4.19 (PIN54_IOR15A_RGB_B3)
/INA1: Pin3.2, U2.12 (INA1), U4.10 (PIN30_IOB13B)
/INA1_2: JP1.2 (B), JP8.2 (B), U3.12 (INA1)
/INA2: Pin2.3, U2.13 (INA2), U4.6 (PIN26_IOB8B)
/INA2_2: JP2.2 (B), JP7.2 (B), U3.13 (INA2)
/INB1: Pin1.2, U2.16 (INB1), U4.3 (PIN36_IOB29B_TF_SCLK)
/INB1_2: JP3.2 (B), JP6.2 (B), U3.16 (INB1)
/INB2: Pin1.3, U2.17 (INB2), U4.2 (PIN37_IOB31A_TF_MOSI)
/INB2_2: JP4.2 (B), JP5.2 (B), U3.17 (INB2)
/PHASEA_1: Pin2.4, U2.14 (PHASEA), U4.5 (PIN25_IOB8A)
/PHASEA_2: U3.14 (PHASEA), U4.21 (PIN56_IOR14A_RGB_G6)
/PHASEB_1: Pin1.1, U2.15 (PHASEB), U4.4 (PIN39_IOB33A_TF_MISO)
/PHASEB_2: U3.15 (PHASEB), U4.20 (PIN55_IOR14B_RGB_G7)
/R1: JP15.2 (B), U5.9 (R1)
/R9: DS1.3 (C_ANODE_1), DS1.8 (C_ANODE_2), JP9.2 (B)
/Reserve_a: Pin2.1, U4.8 (PIN28_IOB11B)
/Reserve_b: Pin3.1, U4.9 (PIN29_IOB13A)
/STANBY_1: Pin1.4, U2.18 (STANDBY), U4.1 (PIN38_IOB31B_TF_CS)
/STANBY_2: U3.18 (STANDBY), U4.17 (PIN51_IOR17B_RGB_B5)
/VCC_1: C4.1, R1.1, U2.8 (VCC)
/VCC_2: C5.1, JP1.1 (A), JP2.1 (A), JP3.1 (A), JP4.1 (A), R2.1, U3.8 (VCC)
/VM: C1.1, C2.1, C3.1, F1.2, R3.1, R4.1, R7.2, R8.2, U2.7 (VM), U3.7 (VM)
/VREF_1: C8.1, R5.1, TP1.1, U2.9 (VREFB), U2.10 (VREFA)
/VREF_2: C9.1, R6.1, TP2.1, U3.9 (VREFB), U3.10 (VREFA)
/VREF_PWM_1: Pin2.2, R5.2, U4.7 (PIN27_IOB11A)
GND: C1.2, C2.2, C3.2, C4.2, C5.2, C6.2, C7.2, C8.2, C9.2, J1.2, J4.9 (5), Rotary_SW1.C, Rotary_SW1.S2, Rotary_SW2.C, Rotary_SW2.S2, SW1.9, SW1.10, SW1.11, SW1.12, SW1.13, SW1.14, SW1.15, SW1.16, U1.2 (GND), U2.1 (GND), U2.3 (GND), U2.6 (GND), U2.19 (GND), U2.22 (GND), U2.24 (GND), U3.1 (GND), U3.3 (GND), U3.6 (GND), U3.19 (GND), U3.22 (GND), U3.24 (GND), U4.26 (GND)
unnamed: C6.1, R1.2, U2.11 (OSCM)
unnamed: C7.1, R2.2, U3.11 (OSCM)
unnamed: DS1.1 (C_E), U4.29 (PIN49_IOR24A_SPILCD_RS), U5.10 (C4)
unnamed: DS1.2 (C_D), U4.28 (PIN31_IOB15A_RGBINIT), U5.11 (C6)
unnamed: DS1.4 (C_C), U4.11 (PIN33_IOB23A_RGB_DE), U5.13 (C1)
unnamed: DS1.5 (C_DP), U4.13 (PIN40_IOB33B_RGB_HS), U5.15 (C7)
unnamed: DS1.6 (C_B), U4.14 (PIN35_IOB29A_RGB_CK), U5.16 (C8)
unnamed: DS1.7 (C_A), U4.37 (HDMI_D2_P), U5.6 (C5)
unnamed: DS1.9 (C_F), U4.34 (HDMI_D1_N), U5.3 (C2)
unnamed: DS1.10 (C_G), JP12.1 (A), U4.35 (HDMI_D1_P)
unnamed: F1.1, J1.1, U1.1 (VIN)
unnamed: J2.1, U2.23 (OUTA-)
unnamed: J2.2, U2.21 (OUTA+)
unnamed: J2.3, U2.2 (OUTB-)
unnamed: J2.4, U2.4 (OUTB+)
unnamed: J3.1, U3.23 (OUTA-)
unnamed: J3.2, U3.21 (OUTA+)
unnamed: J3.3, U3.2 (OUTB-)
unnamed: J3.4, U3.4 (OUTB+)
unnamed: JP5.1 (A), JP9.1 (A), U4.18 (PIN53_IOR15B_RGB_B4)
unnamed: JP8.1 (A), Rotary_SW1.S1, U4.22 (PIN57_IOR13A_RGB_G5)
unnamed: JP10.1 (A), U4.32 (HDMI_D0_N)
unnamed: JP10.2 (B), U5.1 (R5)
unnamed: JP11.1 (A), U4.33 (HDMI_D0_P)
unnamed: JP11.2 (B), U5.2 (R7)
unnamed: JP12.2 (B), U5.4 (C3)
unnamed: JP13.1 (A), U4.38 (PIN76_IOT37B_SPILCD_MCLK)
unnamed: JP13.2 (B), U5.7 (R6)
unnamed: JP14.1 (A), U4.39 (PIN77_IOT37A_SPILCD_MO)
unnamed: JP14.2 (B), U5.8 (R3)
unnamed: JP15.1 (A), U4.30 (PIN48_IOR24B_SPILCD_CS)
unnamed: JP16.1 (A), U4.27 (PIN32_IOB15B_RGBINIT)
unnamed: JP16.2 (B), U5.12 (R4)
unnamed: JP17.1 (A), U4.12 (PIN34_IOB23B_RGB_VS)
unnamed: JP17.2 (B), U5.14 (R2)
unnamed: R3.2, U2.5 (RSB)
unnamed: R4.2, U3.5 (RSB)
unnamed: R6.2, U4.24 (HDMI_CK_P)
unnamed: R7.1, U3.20 (RSA)
unnamed: R8.1, U2.20 (RSA)
unnamed: Rotary_SW2.A, U4.15 (PIN41_IOB41A_RGB_B7)
unnamed: Rotary_SW2.B, U4.16 (PIN42_IOB41B_RGB_B6)
unnamed: Rotary_SW2.S1, U4.48 (PIN63_IOR5A_RGBINIT)
unnamed: J4.4 (8), SW1.1, U4.40 (PIN79_IOT12B_1V8)
unnamed: J4.2 (7), SW1.2, U4.41 (PIN80_IOT12A_1V8)
unnamed: J4.1, SW1.3, U4.42 (PIN81_IOT11B_1V8)
unnamed: J4.3 (2), SW1.4, U4.43 (PIN82_IOT11A_1V8)
unnamed: J4.5 (3), SW1.5, U4.44 (PIN83_IOT10B_1V8)
unnamed: J4.7 (4), SW1.6, U4.45 (PIN84_IOT10A_1V8)
unnamed: J4.8 (10), SW1.7, U4.46 (PIN85_IOT8B_1V8)
unnamed: J4.6 (9), SW1.8, U4.47 (PIN86_IOT8A_BL_PWM_1V8)
unnamed: U4.36 (HDMI_D2_N), U5.5 (R8)

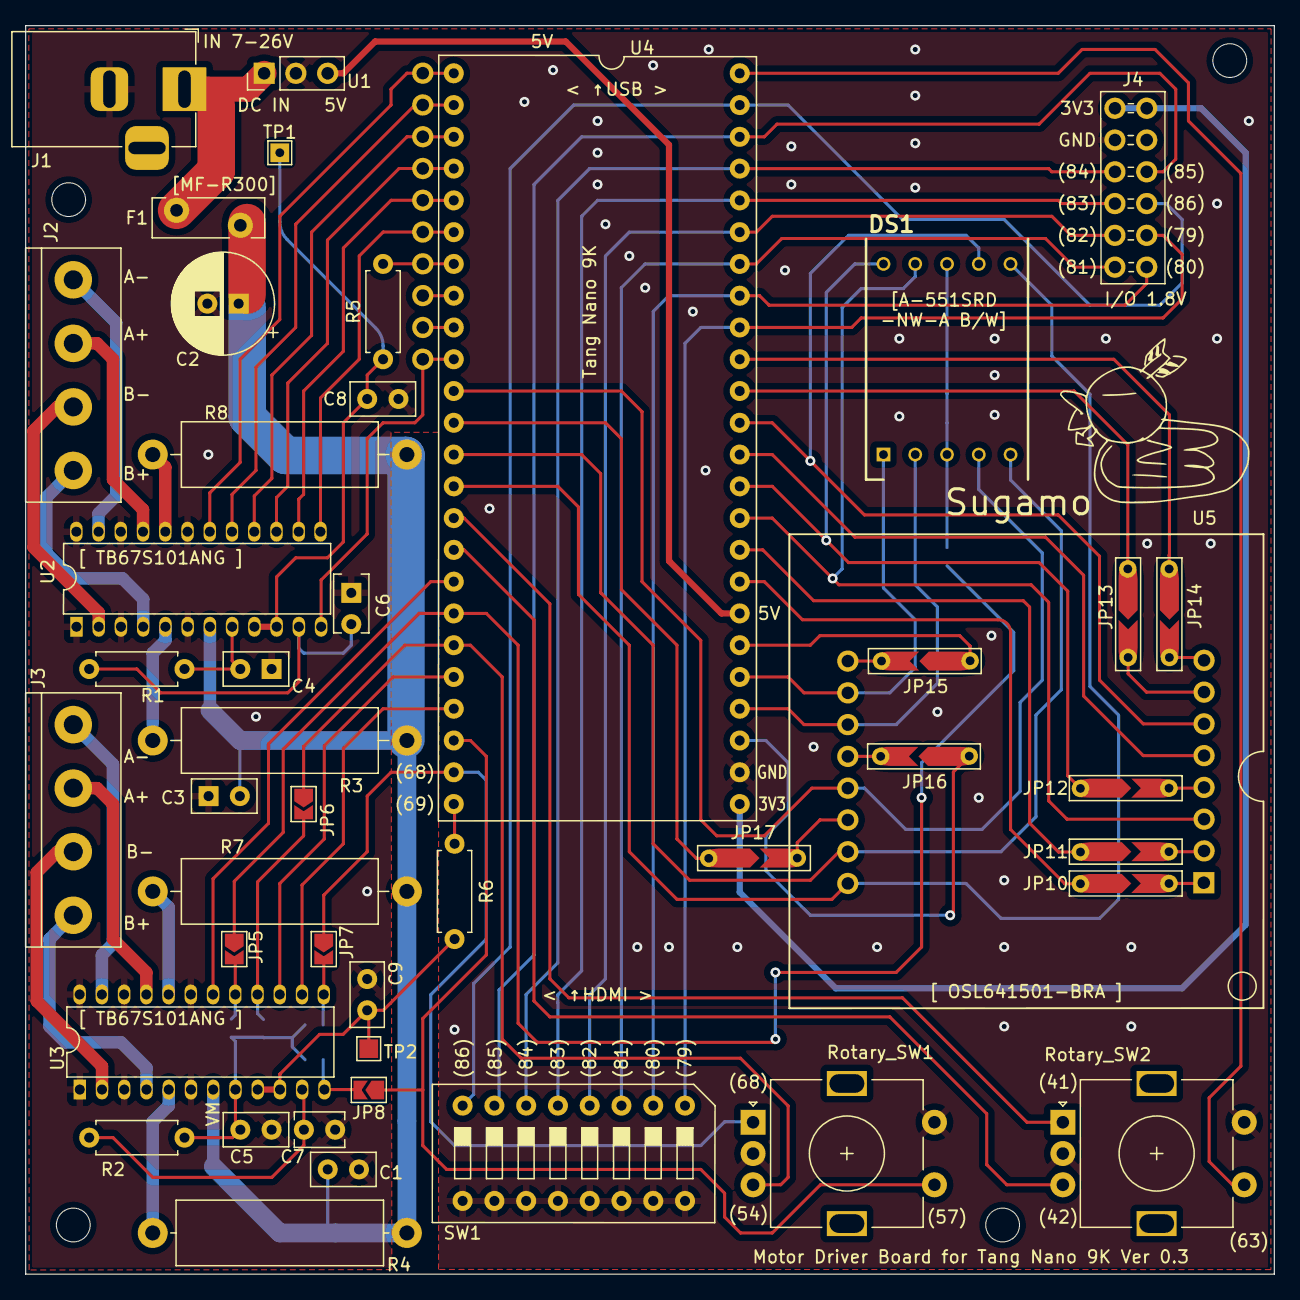
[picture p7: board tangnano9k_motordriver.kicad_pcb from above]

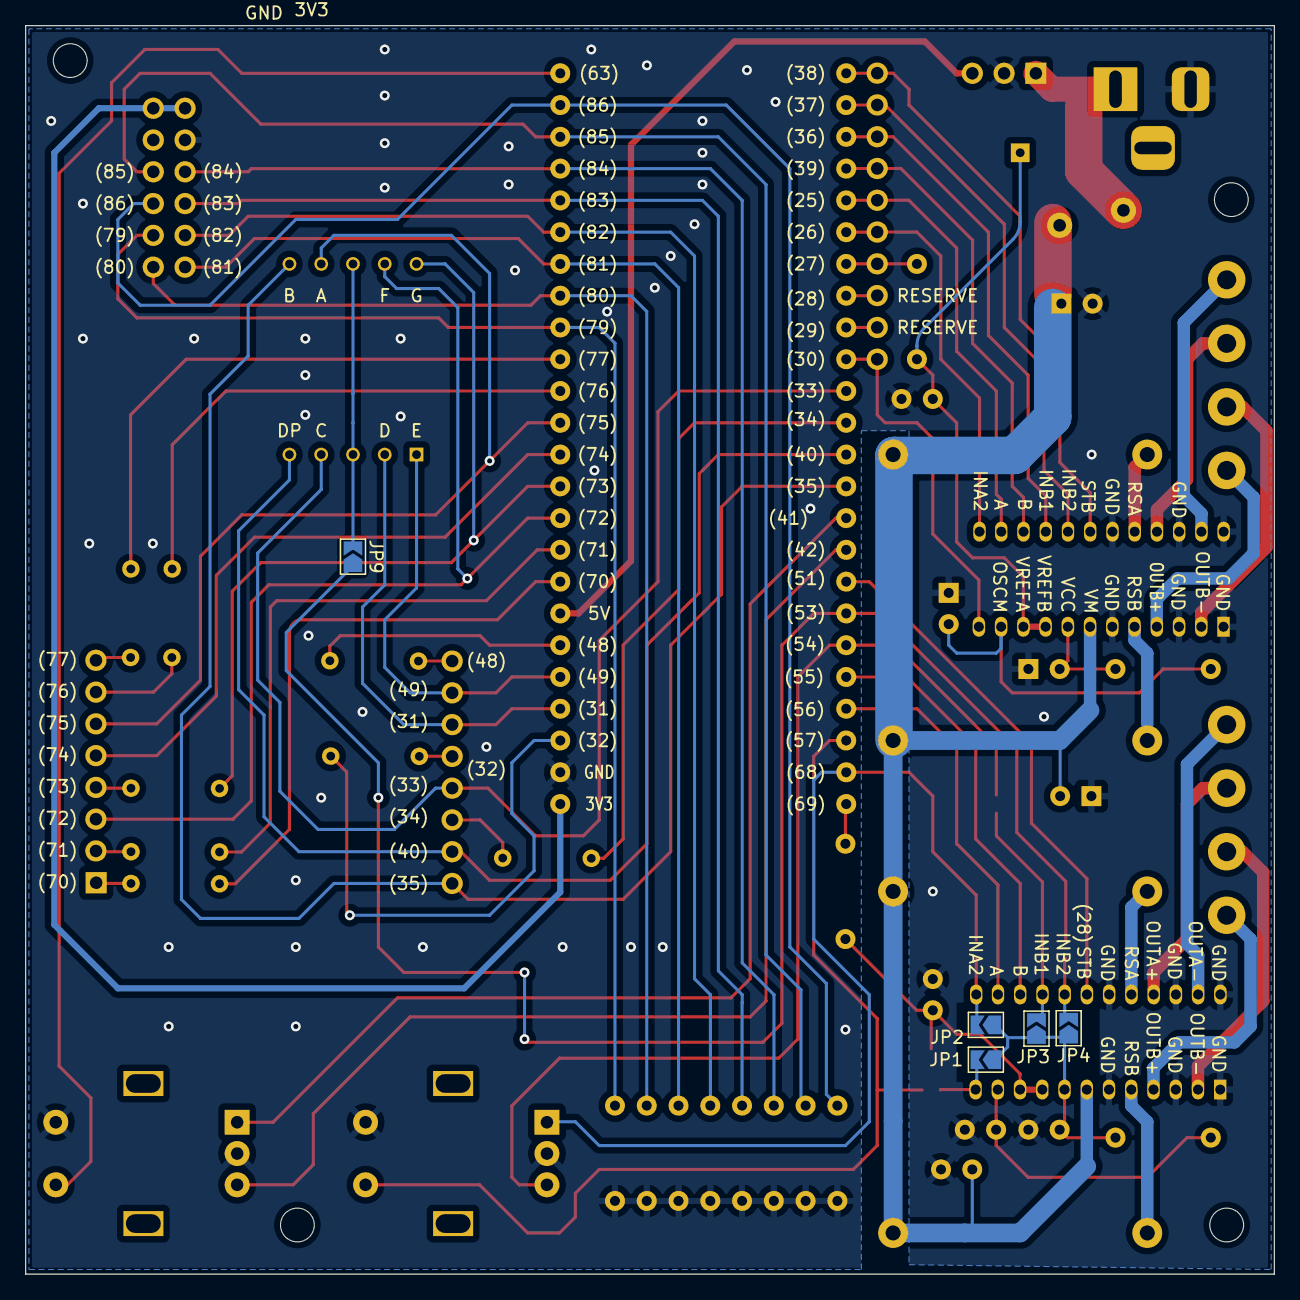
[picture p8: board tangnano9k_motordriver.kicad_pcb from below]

Board: 2 copper layers, 99.8 x 99.8 mm, 53 parts (5 on the bottom side), 81 nets.

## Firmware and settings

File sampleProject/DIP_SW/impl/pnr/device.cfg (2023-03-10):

set JTAG regular_io = false
set SSPI regular_io = true
set MSPI regular_io = true
set READY regular_io = true
set DONE regular_io = false
set RECONFIG_N regular_io = false
set I2C regular_io = false
set CRC_check = true
set compress = false
set encryption = false
set security_bit_enable = true
set bsram_init_fuse_print = true
set background_programming = off
set secure_mode = false
set program_done_bypass = false
set wake_up = 0
set spi_flash_address = 0x00000000
set format = binary
set power_on_reset_monitor = true
set unused_pin = default

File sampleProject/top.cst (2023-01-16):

//Copyright (C)2014-2022 Gowin Semiconductor Corporation.
//All rights reserved.
//File Title: Physical Constraints file
//GOWIN Version: 1.9.8.03 Education
//Part Number: GW1NR-LV9QN88PC6/I5
//Device: GW1NR-9C
//Created Time: Thu 09 08 15:53:57 2022

IO_LOC "ch1_phase_a" 25;
IO_PORT "ch1_phase_a" IO_TYPE=LVCMOS33 PULL_MODE=UP DRIVE=8;
IO_LOC "ch1_phase_b" 39;
IO_PORT "ch1_phase_b" IO_TYPE=LVCMOS33 PULL_MODE=UP DRIVE=8;
IO_LOC "ch1_INB1" 36;
IO_PORT "ch1_INB1" IO_TYPE=LVCMOS33 PULL_MODE=UP DRIVE=8;
IO_LOC "ch1_INB2" 37;
IO_PORT "ch1_INB2" IO_TYPE=LVCMOS33 PULL_MODE=UP DRIVE=8;
IO_LOC "ch1_INA1" 30;
IO_PORT "ch1_INA1" IO_TYPE=LVCMOS33 PULL_MODE=UP DRIVE=8;
IO_LOC "ch1_INA2" 26;
IO_PORT "ch1_INA2" IO_TYPE=LVCMOS33 PULL_MODE=UP DRIVE=8;
IO_LOC "ch1_STANBY" 38;
IO_PORT "ch1_STANBY" IO_TYPE=LVCMOS33 PULL_MODE=UP DRIVE=8;
IO_LOC "ch1_VREF" 27;
IO_PORT "ch1_VREF" IO_TYPE=LVCMOS33 PULL_MODE=UP DRIVE=8;
/*
IO_LOC "2_phase_a" 55;
IO_PORT "2_phase_a" IO_TYPE=LVCMOS33 PULL_MODE=UP DRIVE=8;
IO_LOC "2_phase_b" 56;
IO_PORT "2_phase_b" IO_TYPE=LVCMOS33 PULL_MODE=UP DRIVE=8;
IO_LOC "2_INB1" 54;  //exclusive
IO_PORT "2_INB1" IO_TYPE=LVCMOS33 PULL_MODE=UP DRIVE=8;
IO_LOC "2_INB2" 53;  //exclusive
IO_PORT "2_INB2" IO_TYPE=LVCMOS33 PULL_MODE=UP DRIVE=8;
IO_LOC "2_INA1" 57;  //exclusive
IO_PORT "2_INA1" IO_TYPE=LVCMOS33 PULL_MODE=UP DRIVE=8;
IO_LOC "2_INA2" 68;  //exclusive
IO_PORT "2_INA2" IO_TYPE=LVCMOS33 PULL_MODE=UP DRIVE=8;
IO_LOC "2_STANBY" 51;
IO_PORT "2_STANBY" IO_TYPE=LVCMOS33 PULL_MODE=UP DRIVE=8;
IO_LOC "2_VREF" 69;
IO_PORT "2_VREF" IO_TYPE=LVCMOS33 PULL_MODE=UP DRIVE=8;
*/

IO_LOC "scl" 28;
IO_PORT "scl" IO_TYPE=LVCMOS33 PULL_MODE=UP DRIVE=8 OPEN_DRAIN=ON;
IO_LOC "sda" 29;
IO_PORT "sda" IO_TYPE=LVCMOS33 PULL_MODE=UP DRIVE=8 OPEN_DRAIN=ON;

/*
IO_LOC "cathode[7]" 35;
IO_PORT "cathode[7]" IO_TYPE=LVCMOS33 PULL_MODE=UP DRIVE=8;
IO_LOC "cathode[6]" 40;
IO_PORT "cathode[6]" IO_TYPE=LVCMOS33 PULL_MODE=UP DRIVE=8;
IO_LOC "cathode[5]" 31;
IO_PORT "cathode[5]" IO_TYPE=LVCMOS33 PULL_MODE=UP DRIVE=8;
IO_LOC "cathode[4]" 75;
IO_PORT "cathode[4]" IO_TYPE=LVCMOS33 PULL_MODE=UP DRIVE=8;
IO_LOC "cathode[3]" 49;
IO_PORT "cathode[3]" IO_TYPE=LVCMOS33 PULL_MODE=UP DRIVE=8;
IO_LOC "cathode[2]" 73;
IO_PORT "cathode[2]" IO_TYPE=LVCMOS33 PULL_MODE=UP DRIVE=8;
IO_LOC "cathode[1]" 72;
IO_PORT "cathode[1]" IO_TYPE=LVCMOS33 PULL_MODE=UP DRIVE=8;
IO_LOC "cathode[0]" 33;
IO_PORT "cathode[0]" IO_TYPE=LVCMOS33 PULL_MODE=UP DRIVE=8;
IO_LOC "anode[7]" 74;
IO_PORT "anode[7]" IO_TYPE=LVCMOS33 PULL_MODE=UP DRIVE=8;
IO_LOC "anode[6]" 71;
IO_PORT "anode[6]" IO_TYPE=LVCMOS33 PULL_MODE=UP DRIVE=8;
IO_LOC "anode[5]" 76;
IO_PORT "anode[5]" IO_TYPE=LVCMOS33 PULL_MODE=UP DRIVE=8;
IO_LOC "anode[4]" 70;
IO_PORT "anode[4]" IO_TYPE=LVCMOS33 PULL_MODE=UP DRIVE=8;
IO_LOC "anode[3]" 32;
IO_PORT "anode[3]" IO_TYPE=LVCMOS33 PULL_MODE=UP DRIVE=8;
IO_LOC "anode[2]" 77;
IO_PORT "anode[2]" IO_TYPE=LVCMOS33 PULL_MODE=UP DRIVE=8;
IO_LOC "anode[1]" 34;
IO_PORT "anode[1]" IO_TYPE=LVCMOS33 PULL_MODE=UP DRIVE=8;
IO_LOC "anode[0]" 48;
IO_PORT "anode[0]" IO_TYPE=LVCMOS33 PULL_MODE=UP DRIVE=8;
*/
IO_LOC "boardLED[0]" 10;
IO_PORT "boardLED[0]" IO_TYPE=LVCMOS18 PULL_MODE=UP DRIVE=8;
IO_LOC "boardLED[1]" 11;
IO_PORT "boardLED[1]" IO_TYPE=LVCMOS18 PULL_MODE=UP DRIVE=8;
IO_LOC "boardLED[2]" 13;
IO_PORT "boardLED[2]" IO_TYPE=LVCMOS18 PULL_MODE=UP DRIVE=8;
IO_LOC "boardLED[3]" 14;
IO_PORT "boardLED[3]" IO_TYPE=LVCMOS18 PULL_MODE=UP DRIVE=8;
IO_LOC "boardLED[4]" 15;
IO_PORT "boardLED[4]" IO_TYPE=LVCMOS18 PULL_MODE=UP DRIVE=8;
IO_LOC "boardLED[5]" 16;
IO_PORT "boardLED[5]" IO_TYPE=LVCMOS18 PULL_MODE=UP DRIVE=8;

IO_LOC "clk" 52;
IO_PORT "clk" IO_TYPE=LVCMOS33 PULL_MODE=UP;
/*
IO_LOC "rotary2_a" 68;  //exclusive
IO_PORT "rotary2_a" IO_TYPE=LVCMOS33 PULL_MODE=UP;
IO_LOC "rotary2_b" 54;  //exclusive
IO_PORT "rotary2_b" IO_TYPE=LVCMOS33 PULL_MODE=UP;
IO_LOC "rotary2_SW" 57;  //exclusive
IO_PORT "rotary2_SW" IO_TYPE=LVCMOS33 PULL_MODE=UP;
IO_LOC "rotary1_SW" 63;
IO_PORT "rotary1_SW" IO_TYPE=LVCMOS33 PULL_MODE=UP;
IO_LOC "rotary1_a" 41;
IO_PORT "rotary1_a" IO_TYPE=LVCMOS33 PULL_MODE=UP;
IO_LOC "rotary1_b" 42;
IO_PORT "rotary1_b" IO_TYPE=LVCMOS33 PULL_MODE=UP;
IO_LOC "sw2" 3;
IO_PORT "sw2" IO_TYPE=LVCMOS18 PULL_MODE=UP;
IO_LOC "sw1" 4;
IO_PORT "sw1" IO_TYPE=LVCMOS18 PULL_MODE=UP;
*/
/*7 //seg LED
IO_LOC "LED7seg_anode" 53;  //exclusive
IO_PORT "LED7seg_anode" IO_TYPE=LVCMOS33 PULL_MODE=UP DRIVE=8;
*/
